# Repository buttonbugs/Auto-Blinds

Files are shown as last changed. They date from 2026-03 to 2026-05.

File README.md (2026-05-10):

# Auto Blinds

**Auto Blinds** is an automation project that dynamically adjusts blind orientation based on the Sun's position ([Auto Mode](#auto-mode)). It also includes a mobile interface for convenient remote manual control ([Manual Mode](#manual-mode)).

<sub>*Note:* This `README.md` file includes the introduction of the project. For how to use the code, please visit [SUPPORT.md](/SUPPORT.md).</sub>

## Preview

### Auto Mode

<p align="center">
    <br>
    <sub>Fig. 1. The blinds adjusts the orientation automatically based on time and the Sun's position.</sub>
</p>

### Manual Mode

Auto Blinds provides remote accessibility via smartphone from any distance. Fig. 2 illustrates the Auto Blinds (left) alongside a screen recording of the control interface (right). Users may utilize the on-screen buttons to adjust the blinds to preferred orientations; meanwhile, the dynamic animation provides a real-time preview of the blinds' status, orientation, and the current position of the sun.

<p align="center">
    <a href="https://www.youtube.com/watch?v=zLtPkMw64kk">
        Auto Blinds angle definition
    </a>
    <br>
    <sub>Fig. 2. The Auto Blinds (left) alongside a screen recording of the control interface (right).</sub>
</p>

## Background and Motivation

In my dorm room, my desk and a set of bunk beds are positioned next to a window fitted with east-facing horizontal blinds. The blinds are adjusted using an acrylic hexagonal prism wand. For clarity (Fig. 3), I define 0° as fully tilted down, 90° as horizontal (maximizing outward visibility), and 180° as fully tilted up (minimizing incoming sunlight).

<p align="center">
    Auto Blinds angle definition
    <br>
    <sub>Fig. 3. Auto Blinds angle definition. (a) fully tilted down - 0°. (b) horizontal - 90°. (c) fully tilted up - 180°</sub>
</p>

A nearby building partially affects lighting conditions. Its roof forms an altitude angle of approximately 12° relative to the window (Fig. 4. (a)), which blocks sunlight when the Sun’s altitude is below this threshold (Fig. 4. (b)). However, when the Sun rises above 12°, direct sunlight enters the room unless the blinds are tilted upward (Fig. 4. (c)). This makes it difficult to work comfortably at my desk. At night, exterior lighting shines upward into the room, reflecting off the ceiling (Fig. 4. (d)). In this case, the blinds must be tilted downward to block the light and maintain a suitable sleeping environment. During most of the daytime, however, both my roommate and I prefer the blinds to remain at 90° to allow visibility outside.

<p align="center">
    Altitude angle of the building
    <br>
    <sub>Fig. 4. (a) 12° altitude angle of the building. (b)(c) Different positions of the Sun. (d) Exterior lighting.</sub>
</p>

A practical limitation arises from the bunk bed design: the upper bunk obstructs most of the wand, leaving only about 0.5 inches (1.3 cm) accessible unless I climb onto the bed (Fig. 5). Since the furniture cannot be rearranged, manual adjustment is inconvenient. This motivated the development of a system that enables both autonomous operation (Auto Mode) and remote manual control (Manual Mode).

<p align="center">
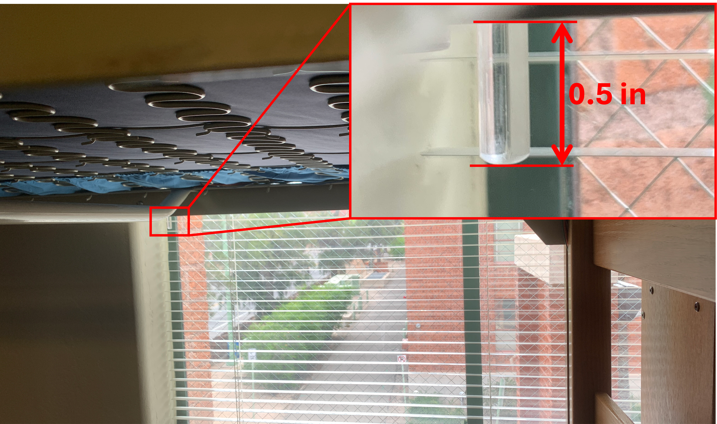
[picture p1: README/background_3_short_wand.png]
The wand of the blinds
    
    <br>
    <sub>Fig. 5. The wand of the blinds.</sub>
</p>

In Auto Mode, a microcontroller retrieves the current date and time from the Internet and calculates the Sun’s position to determine the optimal blind angle. The system also incorporates a simple daily routine, automatically setting the blinds to 0° during sleep hours and 90° upon waking. In Manual Mode, users can remotely set the blind angle or switch between modes via a mobile interface.

## Basic Information

To support reliable network connectivity, particularly with WPA2-Enterprise (university Wi-Fi), an ESP32 microcontroller is used. A 28BYJ-48 stepper motor provides sufficient torque and precise control for rotating the wand. Notion, via its API, serves as an intermediary “server”, enabling communication between mobile devices and the ESP32.

### Electronics

- **Microcontroller:** Seeed Studio XIAO-ESP32-C3 [^1] [^2]

- **Motor:** 28BYJ-48 stepper motor

- **Language:** C++, Notion API

- **Directory:** [src/](src/)

### User Interface

- **Language:** Notion, HTML, JavaScript, CSS

- **Directory:** [docs/status/](docs/status/)

Note: A Notion page, where there are buttons and Notion database, is used as the interface for users to control the blinds on their phones. A [github webpage](docs/status/) is embedded in the Notion page to provide a real-time preview of the orientation of the blinds and the dynamic position of the Sun.

### Algorithm Tests

- **Language:** Python

- **Directory:** [local_debug/](local_debug/)

## 3D Model

This 3D model (Fig. 6) illustrates the motorized blind system and its mounting assembly:

- **Blue Frame:** 3D-printed housing, secured to the bunk frame with **M6x16mm** bolts.
- **Stepper Motor:** A 28BYJ-48 motor (hidden) fastened using **M4x8mm** screws.
- **Motor Driver:** The green ULN2003 module, secured with **M2x12mm** screws.
- **Gearing:** Two blue 3D-printed gears (**10:24** ratio) used to increase output torque.
- **Wand:** A transparent hexagonal prism that controls the blinds.
- **Mounting:** Attaches directly to the vertical white metal frame of the upper bunk.

Click [here](3D_models/auto_blinds_v3.step) to download the 3D model.

<p align="center">
    Wiring
    <br>
    <sub>Fig. 6. Auto Blinds 3D model</sub>
</p>

## Wiring

The wiring diagram (Fig. 7) of this project is relatively straightforward.

- **GPIO4 (D2)** -> IN4
- **GPIO5 (D3)** -> IN3
- **GPIO6 (D4)** -> IN2
- **GPIO7 (D5)** -> IN1

<p align="center">
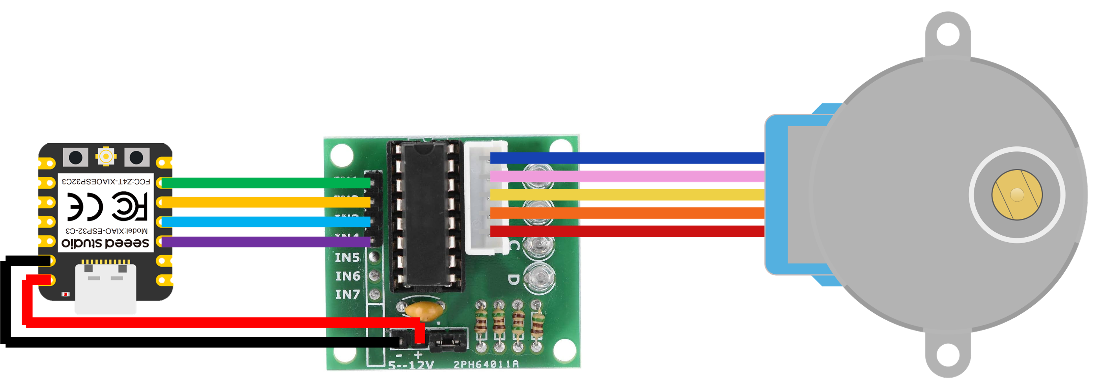
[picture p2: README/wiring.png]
Wiring
    
    <br>
    <sub>Fig. 7. Auto Blinds wiring diagram</sub>
</p>

## Network Communication

Fig. 8 illustrates the network architecture. The ESP32 retrieves commands from the Notion server while concurrently transmitting the blinds' status and the Sun's position. Simultaneously, the Notion app interface synchronizes with the server to reflect real-time updates. Upon user interaction, commands are transmitted from the interface directly to the Notion server. The infrastructure facilitates multi-user concurrency, enabling several individuals to manage the Auto Blinds at the same time.

<p align="center">
    Network Communication
    Network Communication
    <br>
    <sub>Fig. 8. Network architecture for Auto Blinds. (a) Single-user configuration; (b) Multi-user configuration.</sub>
</p>

### Sequence Diagram

```mermaid
sequenceDiagram
    participant user as User
    participant app as Notion App
    participant github as GitHub Webpage
    participant server as Notion Server
    participant esp32_notion as ESP32<br>request_handler.h
    participant esp32_main as ESP32<br>main.cpp
    participant esp32_calc as ESP32<br>sun_calculation.h
    participant esp32_motor as ESP32<br>motor_controller.h
    par ESP32 Notion API
        esp32_main->>esp32_main: Connect to WiFi
        esp32_main->>esp32_notion: Get current status
        esp32_notion->>server: Get current status
        server-->>esp32_notion: Return current status
        esp32_notion->esp32_notion: Get blind angle <br> from current status
        esp32_notion-->>esp32_main: Set "angle"
        Note over server,esp32_main: ESP32 does not have non-volatile storage to <br>store current blind angle, so Notion Server is used <br>to store the angle when the ESP32 is being reset.
        esp32_main->>esp32_notion: Get lastest command
        esp32_notion->>server: Get command list
        server-->>esp32_notion: Return command list
        esp32_notion-->>esp32_notion: Get latest command
        opt
            esp32_notion-)server: Update lastest <br>command status
        end
        esp32_notion-->>esp32_main: Set "target" <br>and "auto_mode"
        esp32_main->>esp32_calc: Get current <br> position of the Sun
        esp32_calc->>esp32_calc: Calculate current <br> position of the Sun
        esp32_calc-->>esp32_main: Set "sun_u", <br>"sun_v", "sun_w"
        alt If auto mode is on
            esp32_main->>esp32_calc: Get "target"
            esp32_calc->>esp32_calc: Calculate "target"
            esp32_calc-->>esp32_main: Set "target"
        end
        esp32_notion->>esp32_motor: Initialize motor
        par ESP32 parallel thread: main.cpp
            loop void loop() in main.cpp
                esp32_main->>esp32_notion: Get lastest command
                esp32_notion->>server: Get command list
                server-->>esp32_notion: Return command list
                esp32_notion-->>esp32_notion: Get latest command
                esp32_notion-)server: Update lastest <br>command status
                opt If Notion App is open
                    server-)app: Send updated database
                    app-)user: Show updated database
                end
                esp32_notion-->>esp32_main: Set "target" <br>and "auto_mode"
                esp32_main->>esp32_calc: Get current <br> position of the Sun
                esp32_calc->>esp32_calc: Calculate current <br> position of the Sun
                esp32_calc-->>esp32_main: Set "sun_u", <br>"sun_v", "sun_w"
                alt If auto mode is on
                    esp32_main->>esp32_calc: Get "target"
                    esp32_calc->>esp32_calc: Calculate "target"
                    esp32_calc-->>esp32_main: Set "target"
                end
                esp32_main->>esp32_notion: Send current status <br>to Notion
                esp32_notion-)server: Update current status
                opt If Notion App is open
                    server-)app: Send current status
                    app->>github: Update current status
                    github->>github: Render preview
                    github->>app: Embed rendered <br>prevew
                    app-)user: Show updated preview
                end
            end
        and ESP32 parallel thread: motor_controller.h
            loop while (true) in motor_controller.h
                esp32_motor->>esp32_main: Get "target"
                esp32_main->>esp32_motor: Return "target"
                esp32_motor->>esp32_motor: Calculate next <br>motor step
                esp32_motor->>esp32_motor: set_motor_phase()
                esp32_motor->>esp32_main: Return "angle"
            end
        end
    and User interference
        opt
            alt
                user->>app: Click a button
                else
                user->>app: Set a specific angle
                else
                user->>app: Calibration
            end
            app->>server: Add command to Notion database
            server-->>app: Return updated database
            app-)user: Show updated database
        end
    end
```

<p align="center">
    <sub>Fig. 9. The sequence diagram of Auto Blinds.</sub>
</p>

## ENU Analemma Calculation

Firstly, the [ecliptic coordinate system](https://en.wikipedia.org/w/index.php?title=Ecliptic_coordinate_system&oldid=1338843308) is used to calculate the Sun’s [declination](https://en.wikipedia.org/w/index.php?title=Declination&oldid=1276361201) ($\delta$), where the origin is the center of the Sun, $X$ points to the vernal equinox, $Z$ is the North Ecliptic Pole, and $Y$ completes the right-handed system. Notably, Jean Meeus’s Algorithm [^3] is used to calculate the approximate time of the vernal equinox in this project (also see [local_debug/analemma_ENU.py](/local_debug/analemma_ENU.py#L10-L57)).

Since

$${\hat{r}}_{SE}=\left[
\begin{matrix}
\cos{\\,\lambda_\odot}\\
\sin{\\,\lambda_\odot}\\
0\\
\end{matrix}
\right]
$$

and

$${\hat{n}}_{NCP}=\left[
\begin{matrix}0\\
-\sin{\\,\varepsilon}\\
\cos{\\,\varepsilon}\\
\end{matrix}
\right],
$$

we have

$$
\begin{aligned}
\sin{\\,\delta}&=\sin{\left[\frac{\pi}{2}-\angle\left(-{\hat{r}}_{SE},{\hat{n}}_{NCP}\right)\right]}\\
&=\cos{\angle(-{\hat{r}}_{SE},{\hat{n}}_{NCP})}\\
&=\frac{{\hat{n}}_{NCP}\bullet(-{\hat{r}}_{SE})}{\left|{\hat{n}}_{NCP}\right|\left|{\hat{r}}_{SE}\right|}\\
&=-\left[\begin{matrix} \cos{\\,\lambda_\odot}\\\\ \sin{\\,\lambda_\odot}\\\\0\end{matrix}\right]\left[\begin{matrix}0\\\\ -\sin{\\,\varepsilon}\\\\ \cos{\\,\varepsilon}\end{matrix}\right]\\
&=\sin{\\,\lambda_\odot}\\,\sin{\\,\varepsilon}.
\end{aligned}
$$

where:

- ${\hat{r}}_{SE}$ is the unit vector pointing from the Sun to Earth in the ecliptic coordinate system

- ${\hat{n}}_{NCP}$ is the unit vector pointing toward the **north celestial pole (NCP)** in the ecliptic coordinate system

- $\delta$ is the Sun’s declination

- $\lambda_\odot$ is the [ecliptic longitude](https://en.wikipedia.org/w/index.php?title=Ecliptic_coordinate_system&oldid=1338843308) of Earth

- $\varepsilon$ is the obliquity of Earth

Since the [subsolar latitude](https://en.wikipedia.org/w/index.php?title=Subsolar_point&oldid=1334981706) ($\phi_s$) is the same as the Sun’s declination ($\delta$), we have

$$\phi_s=\delta=\arcsin{(\sin{\\,\lambda_\odot}\\,\sin{\\,\varepsilon})}$$

In the [Earth-centered, Earth-fixed coordinate system](https://en.wikipedia.org/w/index.php?title=Earth-centered,_Earth-fixed_coordinate_system&oldid=1263086982) (ECEF), the subsolar vector (${\hat{u}}_s$) can be calculated as:

$${\hat{u}}_s=\left[\begin{matrix}\\,\cos{(\phi_s)}\\,\cos{(\lambda_s)}\\\\ \cos{(\phi_s)}\\,\sin{(\lambda_s)}\\\\ \sin{(\phi_s)}\\ \end{matrix}\right]$$

where:

- $\phi_s$ is the subsolar latitude
- $\lambda_s$ is the subsolar longitude, which can be calculated according to the current time ($T_{UTC}$) using the following formula [^4]:

$$\lambda_s=-15\\,(T_{UTC}-12)$$

Similarly, the normalized observer vector (${\hat{u}}_o$), which points directly from the center of Earth to the observer, in ECEF coordinate system can be calculated as:

$${\hat{u}}_o=\left[\begin{matrix}\\,\cos{(\phi_o)}\\,\cos{(\lambda_o)}\\\\ \cos{(\phi_o)}\\,\sin{(\lambda_o)}\\\\ \sin{(\phi_o)}\\ \end{matrix}\right]$$

where:

- $\phi_o$ is the latitude of the observer
- $\lambda_o$ is the longitude of the observer

Note: $ϕ_o$ is the [geodetic latitude](https://en.wikipedia.org/wiki/Geodetic_coordinates) of the observer. However, $ϕ_s$ is the [geocentric latitude](https://en.wikipedia.org/wiki/Latitude#Geocentric_latitude) of the Sun, ignoring the [parallax effect](https://en.wikipedia.org/wiki/Parallax).

Then the coordinate system needs to be transformed into the observer’s coordinate system. The [horizontal coordinate system](https://en.wikipedia.org/w/index.php?title=Horizontal_coordinate_system&oldid=1267888614) is commonly used to represent the position of the sun [^4] [^5]. However, since the blinds and the roof edges mentioned in [Background and Motivation](#background-and-motivation) are parallel to the lines of latitude and longitude, we should use the local [east-north-up](https://en.wikipedia.org/w/index.php?title=Local_tangent_plane_coordinates&oldid=1275515987#Local_east,_north,_up_(ENU)_coordinates) (ENU) coordinate system.

The unit vectors of the **ENU** coordinate system **expressed in** the **ECEF** coordinate system ($\hat{u}$, $\hat{v}$ and $\hat{w}$) can be calculated based on the normalized observer vector (${\hat{u}}_o$):

```math
\begin{aligned}
&\hat{u}=\left[\begin{matrix}u_x&u_y&u_z\\\end{matrix}\right]=\left[\begin{matrix}-\sin{(\lambda_o)}&\cos{(\lambda_o)}&0\\\end{matrix}\right],\\
&\hat{v}=\left[\begin{matrix}v_x&v_y&v_z\\\end{matrix}\right]=\left[\begin{matrix}-\sin{(\phi_o)}\,\cos{(\lambda_o)}&-\sin{(\phi_o)}\,\sin{(\lambda_o)}&\cos{(\phi_o)}\\\end{matrix}\right],\\
&\hat{w}=\left[\begin{matrix}w_x&w_y&w_x\\\end{matrix}\right]={{\hat{u}}_o}^T=\left[\begin{matrix}\cos{(\phi_o)}\,\cos{(\lambda_o)}&\cos{(\phi_o)}\,\sin{(\lambda_o)}&\sin{(\phi_o)}\\\end{matrix}\right].
\end{aligned}
```

where:
$\hat{u}$ is the unit vector pointing to the east
$\hat{v}$ is the unit vector pointing to the north
$\hat{w}$ is the unit vector pointing vertically upward
Subsequently, the Rotation Matrix ($R$) of the coordinate system transformation can be expressed as:

```math
R=\left[\begin{matrix}\hat{u}\\\hat{v}\\\hat{w}\\\end{matrix}\right]=\left[\begin{matrix}-\sin{(\lambda_o)}&\cos{(\lambda_o)}&0\\-\sin{(\phi_o)}\,\cos{(\lambda_o)}&-\sin{(\phi_o)}\,\sin{(\lambda_o)}&\cos{(\phi_o)}\\\cos{(\phi_o)}\,\cos{(\lambda_o)}&\cos{(\phi_o)}\,\sin{(\lambda_o)}&\sin{(\phi_o)}\\\end{matrix}\right]
```

Applying the Rotation Matrix ($R$) to the normalized observer vector (${\hat{u}}_o$) gives the subsolar vector in the ENU coordinate system (${\hat{u}}_s\prime$) [^6]:

```math
{\hat{u}}_s\prime=R{\hat{u}}_s=\left[\begin{matrix}-\sin{(\lambda_o)}&\cos{(\lambda_o)}&0\\-\sin{(\phi_o)}\,\cos{(\lambda_o)}&-\sin{(\phi_o)}\,\sin{(\lambda_o)}&\cos{(\phi_o)}\\\cos{(\phi_o)}\,\cos{(\lambda_o)}&\cos{(\phi_o)}\,\sin{(\lambda_o)}&\sin{(\phi_o)}\\\end{matrix}\right]\left[\begin{matrix}\cos{(\phi_s)}\,\cos{(\lambda_s)}\\\cos{(\phi_s)}\,\sin{(\lambda_s)}\\\sin{(\phi_s)}\\\end{matrix}\right]
```

Let

```math
{\hat{u}}_s\prime=\left[\begin{matrix}s_u\\s_v\\s_w\\\end{matrix}\right],
```

then:

```math
\begin{aligned}
&s_u=-\sin(\lambda_o)\,\cos(\phi_s)\,\cos(\lambda_s)+\cos(\lambda_o)\,\cos(\phi_s)\,\sin(\lambda_s),\\
&s_v=-\sin{(\phi_o)}\,\cos{(\lambda_o)}\,\cos{(\phi_s)}\,\cos{(\lambda_s)}-\sin{(\phi_o)}\,\sin{(\lambda_o)}\,\cos{(\phi_s)}\,\sin{(\lambda_s)}+\cos{(\phi_o)}\,\sin{(\phi_s)},\\
&s_w=s_w=\cos{(\phi_o)}\,\cos{(\lambda_o)}\,\cos{(\phi_s)}\,\cos{(\lambda_s)}+\cos{(\phi_o)}\,\sin{(\lambda_o)}\,\cos{(\phi_s)}\,\sin{(\lambda_s)}+\sin{(\phi_o)}\,\sin{(\phi_s)}.
\end{aligned}
```

Finally, $\arccos{(s_u)}$ is used to represent the solar altitude angle ($a_s\prime$) in the $uw$-plane:

```math
a_s\prime = 
\begin{cases} 
\arccos(s_u) & \text{if } s_w \ge 0\\
-\arccos(s_u) & \text{if } s_w < 0 
\end{cases}
```

## Blind Orientation Calculation

After the Sun rises from the top of the building, the blind target orientation ($θ$) is calculated to block the sunlight.

For simplicity, we let $α$ equal the solar altitude angle ($a_s'$) in the uw-plane and $β$ equal the complementary angle of the blind target orientation ($θ$) in Fig. 10.

<p align="center">
    Target Calculation Image
    <br>
    <sub>Fig. 10. A vertical cross section of the blinds and the sunlight.</sub>
</p>

In Fig. 10, The sunlight is represented by the red line with an arrow, and the cross section of the blinds is represented by the tilted black lines. $AC$ and $BC$ are constants, where $AC$ is the width of a blind and $BC$ is the vertical distance between two blinds.

According to the geometric relations, we have

```math
\begin{aligned}
\angle ABC=\frac{\pi}{2}-\alpha\\
\angle ACB=\beta
\end{aligned}
```

Based on the sum of the interior angles of triangle ABC,

```math
\angle BAC=\pi-\angle ABC-\angle ACB=\frac{\pi}{2}+\alpha-\beta
```

Applying the Law of Sines in triangle ABC,

```math
\frac{BC}{\sin{\left(\frac{\pi}{2}+\alpha-\beta\right)}}=\frac{AC}{\sin{\left(\frac{\pi}{2}-\alpha\right)}}
```

Therefore,

```math
\cos{\left(\alpha-\beta\right)}=\frac{BC}{AC}\cos{\left(\alpha\right)}
```

In this case, $\beta>\alpha$, so

```math
\begin{aligned}
\beta-\alpha=\arccos{\left(\frac{BC}{AC}\cos{\left(\alpha\right)}\right)}\\
\beta=\arccos{\left(\frac{BC}{AC}\cos{\left(\alpha\right)}\right)}-\alpha
\end{aligned}
```

Finally, since $\beta$ equals the complementary angle of the blind target orientation ($\theta$), we have

```math
\theta=\pi-\beta=\pi-\arccos{\left(\frac{BC}{AC}\cos{\left(\alpha\right)}\right)}+\alpha
```

### References

[^1]: “Getting Started with Seeed Studio XIAO ESP32C3 | Seeed Studio Wiki.” Accessed: Feb. 27, 2026. [Online]. Available: https://wiki.seeedstudio.com/XIAO_ESP32C3_Getting_Started/

[^2]: “Amazon.com: Seeed Studio XIAO ESP32C3 - Tiny MCU Board with Wi-Fi and BLE for IoT Controlling Scenarios. Microcontroller with Battery Charge, Power Efficient, and Rich Interface for Tiny Machine Learning. … : Electronics.” Accessed: Feb. 27, 2026. [Online]. Available: https://www.amazon.com/gp/product/B0B94JZ2YF/?th=1

[^3]: J. H. Meeus, [*Astronomical algorithms*](https://dl.acm.org/doi/abs/10.5555/532892). Willmann-Bell, Incorporated, 1991.

[^4]: T. Zhang, P. W. Stackhouse Jr, B. Macpherson, and J. C. Mikovitz, [“A solar azimuth formula that renders circumstantial treatment unnecessary without compromising mathematical rigor: Mathematical setup, application and extension of a formula based on the subsolar point and atan2 function,”](https://www.sciencedirect.com/science/article/pii/S0960148121004031) *Renew. Energy*, vol. 172, pp. 1333–1340, 2021.

[^5]: R. Walraven, [“Calculating the position of the sun,”](https://www.sciencedirect.com/science/article/pii/0038092X7890155X) *Sol. Energy*, vol. 20, no. 5, pp. 393–397, 1978.

[^6]: “Geographic coordinate conversion,” *Wikipedia*. Dec. 22, 2025. Accessed: Mar. 04, 2026. [Online]. Available: https://en.wikipedia.org/w/index.php?title=Geographic_coordinate_conversion&oldid=1328905303#From_ECEF_to_ENU

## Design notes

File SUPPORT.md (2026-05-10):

# Auto Blinds Support

This document includes the usage of the code.

## Getting Started

### secret.h

A header file `secret.h` is necessary to run the code without error. This file includes sensitive information, so please don't forget to add it to `.gitignore` if you are using a git repository.

1. Create `secret.h` in either `/src` or `/include` directory.

2. Add the following code to your `secret.h`. Please note that this is a sample code. You need to adjust it according to your own situation.

```C++
#ifndef ARDUINO_SECRETS_H
#define ARDUINO_SECRETS_H

/* WiFi Configuration */
// WPA2-Enterprise WiFi
#define SECRET_SSID "Your_University_or_Office_SSID"
#define SECRET_USER "Your_WPA2_Username"
#define SECRET_PASS "Your_WPA2_Password"

/* Notion */
#define NOTION_TOKEN "Your_Notion_API_Integration_Token"
#define DATA_SOURCE_ID "Your_data_source_ID"
#define DATABASE_ID "Your_database_ID"

#define NOTION_PREVIEW_BLOCK_ID "Your_Notion_embed_webpage_block_ID"

/* Location */
#define OBSERVER_LATITUDE_DEG 37.334886             // Observer latitude in degrees (Positive: North, Negative: South)
#define OBSERVER_LONGITUDE_DEG -122.008988          // Observer longitude in degrees (Positive: East, Negative: West)
#define TIME_ZONE -8

/* Daily routine */
// Time to wake up
#define wakeup_hour 6
#define wakeup_min 0
#define wakeup_sec 0

// Time to go to sleep
#define sleep_hour 21
#define sleep_min 30
#define sleep_sec 0

#endif
```

### Notion Setup

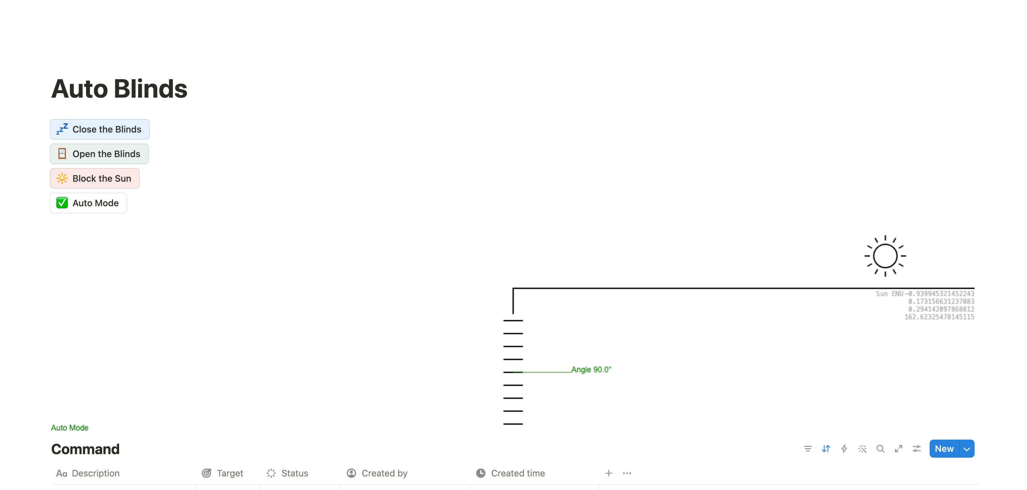
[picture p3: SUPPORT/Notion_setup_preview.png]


1. Create a Notion page wherever you want

2. Give it a name (e.g. `Auto Blinds`)

3. Add several buttons (e.g. `Close the Blinds`, `Open the Blinds`, `Block the Sun`, `Auto Mode`, etc.)

4. Copy and paste the url https://buttonbugs.github.io/Auto-Blinds/status/?auto_mode=true&angle=0&target=0&sun_u=0&sun_v=0&sun_w=1 into the page and select `Embed`

5. Type `/database` and select `Database - Inline`

6. Give it a name (e.g. `Command`)

7. Rename the current property `Name` to `Description`

8. Add the following properties to the database

| Property | Type | Notes |
| - | - | - |
| Target | Number | This is the angle you want the blinds to reach |
| Status | Status | This is the status of the commands |
| Created by | Created by | The person creating the command (**Optional**, but useful when multiple people have access to your Auto Blinds) |
| Created time  | Created time  | When the command is created (**Optional**, but useful when multiple people have access to your Auto Blinds) |

Note: Please **DO NOT** change the property name unless you change it in `notion_handler.cpp` as well.

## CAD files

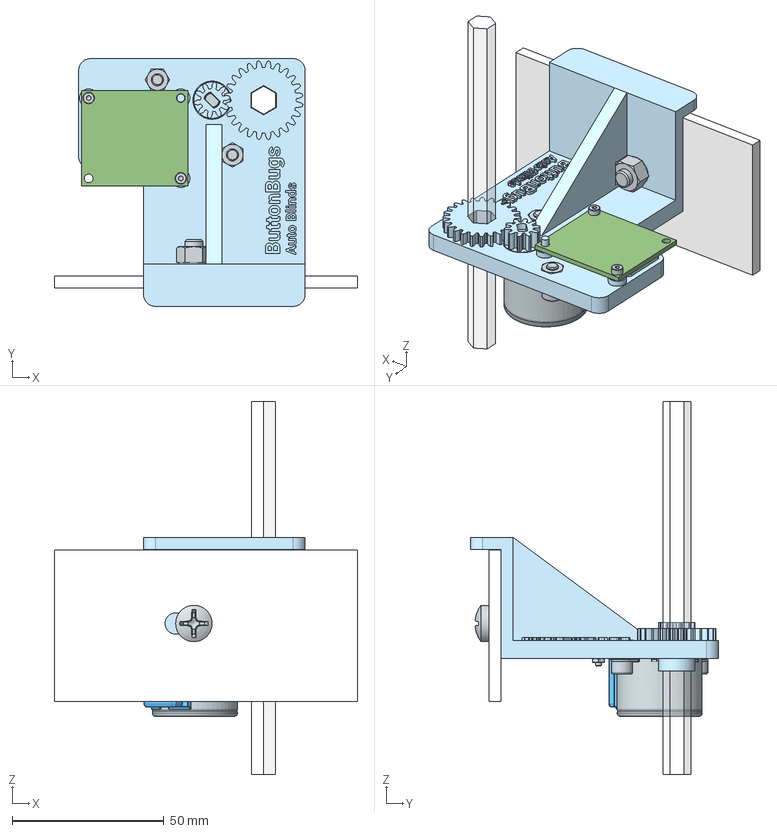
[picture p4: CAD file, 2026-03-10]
3D_models/auto_blinds_v3.step
100.0 x 81.7 x 123.0 mm
won9329C2FD5x4mz x 8
Hex socket head cap screw M4x0.70 x 8 x 2
ULN2003
Main_v3
Hex nut grade A & B M6x1.0
Hex thin nut grade A & B M2 x 2
Hexagon
Hex thin nut grade A & B M4 x 2
Hex socket head cap screw M2x0.40 x 12 x 2
Hex_Connector_v3
PH Pan head screw M6x1.00 x 16
Bed Board Side
Motor_Connector_v3

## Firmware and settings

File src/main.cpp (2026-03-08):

// Arduino
#include <Arduino.h>

// Libraries
#include <map>                  // Required for handling headers elegantly

// Your Header Files
#include "config.h"
#include "wifi_handler.h"       // To handle wifi connection
#include "notion_handler.h"
#include "motor_controller.h"
#include "sun_calculation.h"

bool auto_mode = true;
float angle = 0;                    // Current angle of the blinds in degrees
float target = 0;
double sun_u = 0;
double sun_v = 0;
double sun_w = 0;

String page_id = "";                // The Notion page_id of the lastest command

void setup() {
    Serial.begin(9600);
    delay(200);                   // Give serial monitor time to open

    // Connect to WiFi
    connect_to_wifi();
    init_time();

    // Get Current status
    Serial.println("Get Current status");
    angle = download_current_status();

    // Get latest Command
    if(get_latest_command(&auto_mode, &angle, &target, &page_id)) {
        Serial.println("Get Latest Command Success");
    } else {
        Serial.println("Get Latest Command Fail");
    }

    get_sun_position_ENU(&sun_u, &sun_v, &sun_w);
    if (auto_mode) {
        target = get_auto_mode_target(sun_u, sun_v, sun_w);
    }
    
    init_motor_controller(&angle, &target);

    // sun calcuation test
    delay(500);
}

void loop() {
    // Get latest Command
    if(get_latest_command(&auto_mode, &angle, &target, &page_id)) {
        // Serial.println("Get Latest Command Success");
    } else {
        // Serial.println("Get Latest Command Fail");
    }
    
    get_sun_position_ENU(&sun_u, &sun_v, &sun_w);
    if (auto_mode) {
        target = get_auto_mode_target(sun_u, sun_v, sun_w);
    }

    // Serial.println("Update Status");
    upload_current_status(auto_mode, angle, target, sun_u, sun_v, sun_w);
    Serial.printf("auto_mode: %d, angle: %f, target: %f, sun_u: %.15lf, sun_v: %.15lf, sun_w: %.15lf\n", auto_mode, angle, target, sun_u, sun_v, sun_w);
    
    // Delay
    delay(request_delay_ms);
}

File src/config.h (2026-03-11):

#ifndef CONFIG_H
#define CONFIG_H

/* Calculation */
#define EARTH_OBLIQUITY 23.44       // deg, Earth obliquity (axial tilt)
#define SECONDS_PER_DAY 86400       // The number of seconds per day
#define SECONDS_PER_HOUR 3600       // The number of seconds per hour

/* Pin config */
// Stepper motor signal pins
// from PIN_1 to PIN_4 is the sequence of opening the blinds
// from PIN_4 to PIN_1 is the sequence of closing the blinds
#define MOTOR_PIN_1 4               // GPIO4 = D2
#define MOTOR_PIN_2 5               // GPIO5 = D3
#define MOTOR_PIN_3 6               // GPIO6 = D4
#define MOTOR_PIN_4 7               // GPIO7 = D5

/* Physical config */
#define total_step 46080            // Total steps for the blinds to turn 180 degrees
#define step_duration_ms 5          // Interval for toggling motor step in milliseconds
#define building_angle_deg 11.5     // The altitude angle of the top of the building in front of the blinds in degrees

// blind_width and blind_spacing can be in any unit you want (e.g. mm, inches, meters),
// but they should be in the same unit.
// Here, millimeter is used as an example.
#define blind_width 25.0            // The width of a blind
#define blind_spacing 21.5          // The vertical distance between two blinds

/* Software */
#define request_delay_ms 10         // Delay between two groups of Notion API requests in millisenconds

/* Daily routine */
#define event_time_offset_s 30      // The target will change this much time in advance before an event in your daily routine

#endif

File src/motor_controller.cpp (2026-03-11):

#include <Arduino.h>
#include <freertos/FreeRTOS.h>
#include <freertos/task.h>

#include "config.h"

float* angle_pt_local;
float* target_pt_local;
int current_step = 0;
int target_step = 0;

void set_motor_phase(int phase) {
    digitalWrite(MOTOR_PIN_1, phase == 0);
    digitalWrite(MOTOR_PIN_2, phase == 1);
    digitalWrite(MOTOR_PIN_3, phase == 2);
    digitalWrite(MOTOR_PIN_4, phase == 3);
}

void set_interval(void *pvParameters) {
    set_motor_phase(current_step % 4);
    while (true) {
        // Calculate target_step
        target_step = (*target_pt_local) * total_step / 180;

        // Compare target_step and current_step to increase or decrease current_step
        if (target_step > current_step) {
            current_step++;
            set_motor_phase(current_step % 4);

        } else if (target_step < current_step) {
            current_step--;
            set_motor_phase(current_step % 4);

        } else {
            // Deactivate the motor (turn off the LEDs)
            set_motor_phase(5);
        }

        // Update angle so that it can be synced to Notion preview
        *angle_pt_local = current_step * 180.0F / total_step;

        // Delay step_duration_ms. Do not use delay(step_duration_ms)
        vTaskDelay(pdMS_TO_TICKS(step_duration_ms)); // Non-blocking delay
    }
}

void init_motor_controller(float * angle_pt, float * target_pt) {
    angle_pt_local = angle_pt;
    target_pt_local = target_pt;

    current_step = (*angle_pt_local) * total_step / 180;
    target_step = (*target_pt_local) * total_step / 180;
    /* Set Pin Mode */
    pinMode(MOTOR_PIN_1, OUTPUT);
    pinMode(MOTOR_PIN_2, OUTPUT);
    pinMode(MOTOR_PIN_3, OUTPUT);
    pinMode(MOTOR_PIN_4, OUTPUT);
    xTaskCreate(set_interval, "motor", 2048, NULL, 1, NULL);
}

void calibration(float calibration_angle) {
    current_step = calibration_angle * total_step / 180;
}

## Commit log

2026-02-13 Build PIO ESP32 Framework
2026-02-14 Use ESP32 to read Notion Database
2026-02-28 README Citation for ESP32
2026-03-06 Uploat current status to Notion embed block
2026-03-07 Improve text rendering; change total_step config; remove unnecessary Serial print
2026-03-07 Fix Android appearance issue
    [config.h, main.cpp, notion_handler.cpp]
2026-03-07 Add calibration
2026-03-07 Fix notion preview dark mode appearance issue
    [config.h]
2026-03-10 Improve: swap the position of "User interference" and "ESP32 Notion API" in README.md
2026-03-10 Improve: expand ESP32 threads in the sequence diagram in README.md
2026-03-10 Add: motor reactivation
2026-03-10 Add: 3D model
    [auto_blinds_v3.step]
2026-03-11 Add: Wiring
2026-03-11 Remove: motor deactivation
2026-05-10 Insert YouTube video link in README.md
2026-05-10 Add wiring diagram description in README.md
